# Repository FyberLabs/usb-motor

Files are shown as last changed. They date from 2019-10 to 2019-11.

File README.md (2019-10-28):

# usb-motor driver
Variation on the [Small Multicell USB Type C Charger](https://hackaday.io/project/85465-small-multicell-usb-type-c-charger), but with a specific purpose of making USB powered tools.
There will be a brushless version eventually and a few other application variations.
It supports a variety of rechargeable batteries and 1-4 cells depending on the solder bridge configuration.

For right now it has a single power/action button that can turn on/off, change speed, and reverse direction.
A capacitive trigger or other more precise control can be added.
There is also a reset button that can be removed after development.

These boards should 'mostly' stack in a 1x1.5" space with only a few wiring problems between them.
This design has excessive FET control and filtering which can be reduced.
Ideally, the design should fit on a single 1x1.5" board when developed for a specific application.

[Submitted gerbers to oshpark](https://oshpark.com/shared_projects/w56T8NJs])

front

back  

[Assembly BOM](http://htmlpreview.github.com/?https://github.com/FyberLabs/usb-motor/blob/master/bom/ibom.html)
Generated By [InteractiveHtmlBom](https://github.com/openscopeproject/InteractiveHtmlBom)  

GPL licensed firmware will be coming for the CCG3.  I expect to use stock TI firmware for TI chips.

Notes:
* There will be bugs in the hardware and eventually they will hopefully be found and 'fixed.
* There are many solderbridges to disable FET controls and select cell counts as necessary.
* The CC 5V line on CCG3 should be routed or the 3v3 supply made 5V to fully enable a powerbank/OTG capabilities.
* Initial testing of some of the boards, so some logic may be incorrect.
* Developed with extra small designator silkscreen fonts which are likely to fail most PCB processes.  
(They are not that important to my build process, and usually make a mess of the silkscreen either way.)
* First panel attempted through oshpark  
(Usually I remove edge lines on mousebites for other fabs, though this variation does make copper zones in KiCAD work better.)

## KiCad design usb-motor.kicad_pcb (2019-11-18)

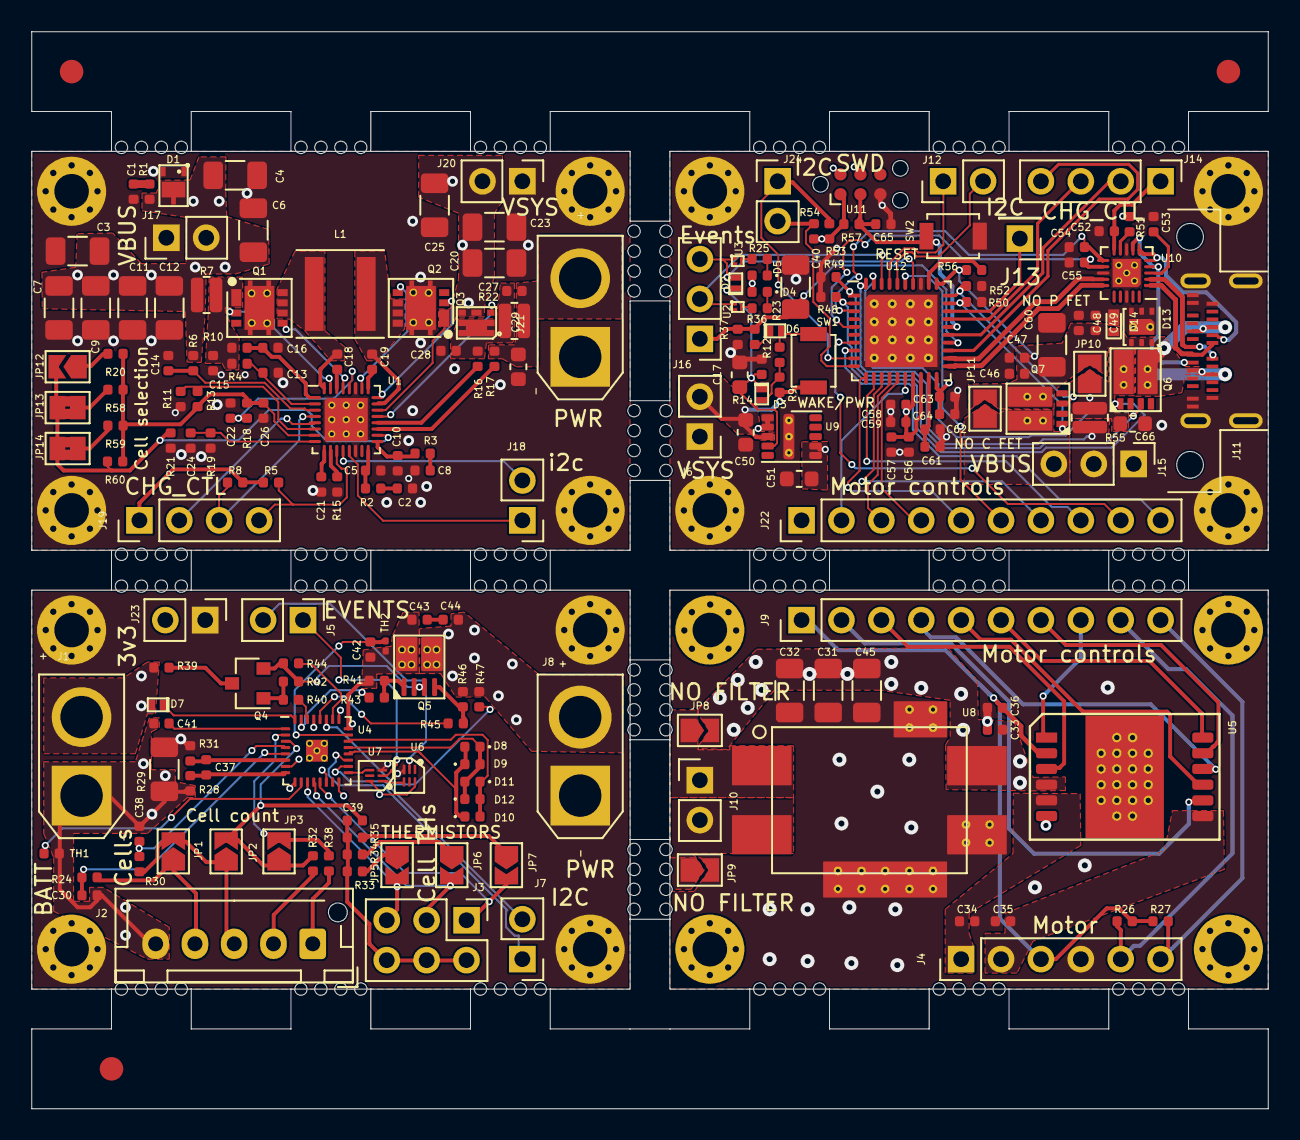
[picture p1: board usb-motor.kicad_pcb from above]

Board: 4 copper layers, 78.7 x 68.6 mm, 252 parts (0 on the bottom side), 128 nets.

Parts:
C1, C26, C28, C52, C57, C58, C61, C63: 1uF; C_0402_1005Metric
C2: 1800pF; C_0402_1005Metric
C3, C4, C6, C7, C9, C11, C12, C20, C23, C25, C31, C32, C40, C45: 22uF; C_1206_3216Metric
C5: 33pF; C_0402_1005Metric
C8: 680pF; C_0402_1005Metric
C10: 15pF; C_0402_1005Metric
C13, C14: 0.033uF; C_0402_1005Metric
C15, C46, C47, C48, C49: 0.01uF; C_0402_1005Metric
C16: 0.47uF; C_0402_1005Metric
C17, C29, C50: 10uF; C_0603_1608Metric
C18, C19: 0.047uF; C_0402_1005Metric
C21, C24: 100pF; C_0402_1005Metric
C22, C41: 2.2uF; C_0402_1005Metric
C27, C30, C33, C36, C37, C38, C39, C42, C43, C53, C56, C59, C62, C64, C65: 0.1uF; C_0402_1005Metric
C34, C35: 27nF; C_0402_1005Metric
C44: 0.22uF; C_0402_1005Metric
C51: 22uF+ 6.3V; C_0603_1608Metric
C54, C55: 390pF; C_0402_1005Metric
C60: 10uF; C_1206_3216Metric
C66: 1uF; C_0603_1608Metric
D1: ESDA22P150-1U3M; QFN-3 (ESDA22P150-1U3M)
D2, D3, D6, D7: BAS40LP-7; D_402
D4: VLMG1500-GS08; LED_0402_1005Metric
D5: VLMO1500-GS08; LED_0402_1005Metric
D8, D9, D10, D11, D12: VLMB1500-GS08; LED_0402_1005Metric
D13: TVS2200; TVS2200-DRV0006A-WSON-2x2
D14: NSR20F30NXT5G; DSN2(0603)
FID1, FID2, FID3: Fiducial; Fiducial_1.5mm_Mask3mm
H1, H2, H3, H4, H5, H6, H7, H8, H9, H10, H11, H12, H13, H14, H15, H16: M; MountingHole_2.2mm_M2_Pad_Via
J1: BATT; AMASS_XT30U-M_1x02_P5.0mm_Vertical
J2: Cells; JST_XH_B5B-XH-AM_1x05_P2.50mm_Vertical
J3: Cell THs; PinHeader_2x03_P2.54mm_Vertical
J4: Motor; PinHeader_1x06_P2.54mm_Vertical
J5: EVENTS; PinHeader_1x02_P2.54mm_Vertical
J6, J20: VSYS; PinHeader_1x02_P2.54mm_Vertical
J7, J12, J24: I2C; PinHeader_1x02_P2.54mm_Vertical
J8: PWR; AMASS_XT30U-F_1x02_P5.0mm_Vertical
J9, J22: Motor controls; PinHeader_1x10_P2.54mm_Vertical
J10: Power; PinHeader_1x02_P2.54mm_Vertical
J11: USB_C_Receptacle; USB_C_Receptacle_Amphenol_124018792112A
J13: xpins; PinHeader_1x01_P2.54mm_Vertical
J14, J19: CHG_CTL; PinHeader_1x04_P2.54mm_Vertical
J15: VBUS; PinHeader_1x03_P2.54mm_Vertical
J16: Events; PinHeader_1x03_P2.54mm_Vertical
J17: VBUS; PinHeader_1x02_P2.54mm_Vertical
J18: i2c; PinHeader_1x02_P2.54mm_Vertical
J21: PWR; AMASS_XT30U-M_1x02_P5.0mm_Vertical
J23: 3v3; PinHeader_1x02_P2.54mm_Vertical
JP1, JP2, JP3, JP5, JP6, JP7: SolderJumper_2_Open; SolderJumper-2_P1.3mm_Open_TrianglePad1.0x1.5mm
JP8, JP9: NO FILTER; SolderJumper-2_P1.3mm_Open_TrianglePad1.0x1.5mm
JP10: NO P FET; SolderJumper-2_P1.3mm_Open_TrianglePad1.0x1.5mm
JP11: NO C FET; SolderJumper-2_P1.3mm_Open_TrianglePad1.0x1.5mm
JP12: 4th; SolderJumper-2_P1.3mm_Open_TrianglePad1.0x1.5mm
JP13: 3rd; SolderJumper-2_P1.3mm_Bridged2Bar_Pad1.0x1.5mm
JP14: 2nd; SolderJumper-2_P1.3mm_Bridged2Bar_Pad1.0x1.5mm
L1: 2.2uH; L_Coilcraft_XAL5030
MOU1, MOU2, MOU3, MOU4, MOU5, MOU6, MOU7, MOU8, MOU9, MOU10, MOU11, MOU12, MOU13, MOU14, MOU15, MOU16, MOU17, MOU18, MOU19, MOU20, MOU21, MOU22, MOU23, MOU24, MOU25, MOU26, MOU27, MOU28, MOU29, MOU30, MOU31, MOU32: Mousebite; mousebites
Q1, Q2: CSD87333Q3D
Q3: FDMA6676PZ; MicroFET
Q4: FDN358P; SOT-23
Q5: CSD87313DMS
Q6, Q7: CSD87503Q3E
R1: 2.2 0.5W; R_0402_1005Metric
R2: 40.2k; R_0402_1005Metric
R3, R23, R25, R26, R27, R33, R34, R35, R36, R47: 10.0k; R_0402_1005Metric
R4, R6: 4.99; R_0402_1005Metric
R5, R8: 3.83k; R_0402_1005Metric
R7, R22, R55: 10m; KRL2012E(0508)
R9, R12: 270k; R_0402_1005Metric
R10: 1.0; R_0402_1005Metric
R11, R13, R14, R21, R37, R51: 100k; R_0402_1005Metric
R15: 30k; R_0402_1005Metric
R16, R17, R18: 10; R_0402_1005Metric
R19: 137k; R_0402_1005Metric
R20: 56-57k; R_0402_1005Metric
R24, R28, R30, R31, R32, R38, R44, R56: 100; R_0402_1005Metric
R29: 0.001; R_1206_3216Metric
R39: 300; R_0402_1005Metric
R40, R43, R45: 5.1k; R_0402_1005Metric
R41, R42, R46, R48, R49, R50, R52: 10.0M; R_0402_1005Metric
R53, R54: 2.2k; R_0402_1005Metric
R57: 4.7k; R_0402_1005Metric
R58: 169k; R_0402_1005Metric
R59: 280k; R_0402_1005Metric
R60: 300k; R_0402_1005Metric
SW1: WAKE/PWR; SW_SPST_B3U-1000P
SW2: RESET; SW_SPST_B3U-1000P
TH1: 103; R_0402_1005Metric
TH2: 10.0k; R_0201_0603Metric
U1: BQ25713(B); QFN-32_EP2.8_4x4_Pitch0.4mm
U2, U3: CSD15380F3; PICOSTAR (YJM)
U4: BQ4050R; QFN-32_EP1.4_4x4_Pitch0.4mm
U5: IFX9201SG; PG-DSO-12-17
U6: SN74LVC1G14D; TI-DSF0006A-SON-5P-SN74xx
U7: SN74LVC1G08D; TI-DSF0006A-SON-5P-SN74xx
U8: BNX02x
U9: LMZM23601V3; Texas_SIL0010A_MicroSiP-10-1EP_3.8x3mm_P0.6mm_EP0.7x2.9mm_T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
U10: TPD6S300A; QFN-20_EP1.8_3x3_Pitch0.4mm
U11: SWD; Tag-Connect_TC2030-IDC-NL_2x03_P1.27mm_Vertical
U12: CYPD3123-40LQXIT; QFN-40_EP_6x6_Pitch0.5mm

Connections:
+3V3: C51.2, C63.2, C64.2, D4.2, D5.2, J23.2, R51.2, U6.5, U7.5, U9.6, U9.7, U12.20
-BATT: C30.1, C38.1, C39.1, C41.1, J1.1, J2.5, J3.2, J3.4, J3.6, R28.2, R29.2, R33.1, R34.1, R35.1, TH1.2, U4.7, U4.9, U4.14, U4.16, U4.25, U4.29, U4.33
/4 Cell Charger/1c: J2.4, JP1.1, R24.2
/4 Cell Charger/2c: J2.3, JP1.2, JP2.1, R30.2
/4 Cell Charger/3c: J2.2, R32.2
/4 Cell Charger/BBAT: D7.1, U4.32
/4 Cell Charger/C43-44: C43.2, C44.1
/4 Cell Charger/CHG: R43.1, U4.31
/4 Cell Charger/DSG: R45.1, U4.28
/4 Cell Charger/JP5: JP5.1, R33.2
/4 Cell Charger/JP6: JP6.1, R34.2
/4 Cell Charger/JP7: JP7.1, R35.2
/4 Cell Charger/LEDA: D8.2, D9.1, D10.1, U4.20
/4 Cell Charger/LEDB: D8.1, D9.2, D11.2, D12.1, U4.21
/4 Cell Charger/LEDC: D10.2, D11.1, D12.2, U4.22
/4 Cell Charger/PACK: R47.2, U4.27
/4 Cell Charger/PBI: C41.2, U4.1
/4 Cell Charger/PCHG: R40.2, U4.30
/4 Cell Charger/PTC: C42.1, TH2.1, U4.23
/4 Cell Charger/R39: Q4.3, R39.1
/4 Cell Charger/R40: Q4.1, R40.1, R42.1
/4 Cell Charger/R43: Q5.1, R41.1, R43.2
/4 Cell Charger/R45: Q5.4, R45.2, R46.1
/4 Cell Charger/SRN: C37.1, R31.1, U4.6
/4 Cell Charger/SRP: C37.2, R28.1, U4.8
/4 Cell Charger/TS1: TH1.1, U4.10
/4 Cell Charger/TS2: J3.5, JP5.2, U4.11
/4 Cell Charger/TS3: J3.3, JP6.2, U4.12
/4 Cell Charger/TS4: J3.1, JP7.2, U4.13
/4 Cell Charger/VC1: C30.2, R24.1, U4.5
/4 Cell Charger/VC2: C38.2, R30.1, U4.4
/4 Cell Charger/VC3: C39.2, JP2.2, JP3.1, R32.1, U4.3
/4 Cell Charger/VC4: JP3.2, R38.1, U4.2
/4 Cell Charger/VCCQ: Q4.2, Q5.2, Q5.3, R42.2, R44.2
/4 Cell Charger/VCCcell: R44.1, U4.26
/4 Cell Charger/~DISP: U4.17, U7.4
/4 Cell Charger/~SW_SIG: U6.4, U7.1
/6-36V: C42.2, C43.1, D7.2, J1.2, J2.1, J10.1, JP8.1, Q5.8, R38.2, R39.2, R41.2, TH2.2, U4.24, U8.B
/BAT_OUT: C27.2, C29.1, C44.2, J8.2, J21.2, Q5.5, R17.1, R22.1, R46.2, R47.1
/Brushed 12V Motor/36V: C31.2, C32.1, C33.1, C45.2, JP8.2, U5.4, U8.CB
/Brushed 12V Motor/GNDF: C31.1, C32.2, C33.2, C34.2, C35.2, C36.2, C45.1, J4.4, JP9.2, U5.6, U8.CG
/Brushed 12V Motor/M1: C34.1, J4.1, U5.5
/Brushed 12V Motor/M2: C35.1, J4.2, U5.7
/CHRG_OK: J14.3, J19.3, R8.1, U1.4, U12.27
/CSN: J9.5, J22.5, U5.9, U12.11
/DIR: J9.8, J22.8, U5.1, U11.4, U12.12
/DIS: J9.7, J22.7, U5.11, U11.2, U12.13
/EN_OTG: J14.2, J19.2, U1.5, U12.25
/GPIO13: J13.1, U12.28
/PROCHOT: J14.4, J19.4, R5.1, U1.11, U12.23
/PWM: J9.6, J22.6, U5.12, U12.35
/SCK: J9.4, J22.4, U5.10, U12.15
/SCL: J7.1, J18.1, J24.1, R53.2, U1.13, U4.19, U12.9
/SDA: J7.2, J18.2, J24.2, R54.2, U1.12, U4.18, U12.10
/SENSA: J4.5, J9.9, J22.9, R26.2, U12.7
/SENSB: J4.6, J9.10, J22.10, R27.2, U12.8
/SI: J9.2, J22.2, U5.8, U12.16
/SNK_EVENT: D2.2, J5.1, J16.3, U3.1, U7.2, U12.34
/SO: J9.3, J22.3, U5.3, U12.14
/SW_SIG: C40.2, J5.2, J16.1, R36.2, R37.1, U6.2, U12.24
/USB Buck Boost/ACN: C13.1, R4.1, U1.2
/USB Buck Boost/ACP: C14.1, R6.1, U1.3
/USB Buck Boost/CELL_PREZ: JP12.2, JP13.2, JP14.2, R21.1, R60.2, U1.18
/USB Buck Boost/COMP1: C5.1, R2.2, U1.16
/USB Buck Boost/COMP1T: C2.1, R2.1
/USB Buck Boost/COMP2: C10.1, R3.2, U1.17
/USB Buck Boost/COMP2TT: C8.1, R3.1
/USB Buck Boost/HIDRV1: Q1.3, U1.31
/USB Buck Boost/HIDRV2: Q2.3, U1.24
/USB Buck Boost/IADPT: C24.1, R19.1, U1.8
/USB Buck Boost/IBAT: C21.1, U1.9
/USB Buck Boost/ILIM: R11.1, R13.1, U1.6
/USB Buck Boost/JP12: JP12.1, R20.2
/USB Buck Boost/JP13: JP13.1, R58.2
/USB Buck Boost/JP14: JP14.1, R59.2
/USB Buck Boost/LODRV1: Q1.5, U1.29
/USB Buck Boost/LODRV2: Q2.5, U1.26
/USB Buck Boost/PSYS: R15.1, U1.10
/USB Buck Boost/REGN: C22.1, R18.2, U1.28
/USB Buck Boost/SRN: R17.2, U1.19
/USB Buck Boost/SRP: R16.2, U1.20
/USB Buck Boost/SRP_R: C27.1, C28.1, Q3.1, Q3.2, Q3.5, Q3.6, Q3.8, R16.1, R22.2
/USB Buck Boost/SW1: C18.1, L1.1, Q1.6, Q1.7, Q1.8, U1.32
/USB Buck Boost/SW2: C19.1, L1.2, Q2.6, Q2.7, Q2.8, U1.23
/USB Buck Boost/TST1: C18.2, U1.30
/USB Buck Boost/TST2: C19.2, U1.25
/USB Buck Boost/VBUS_D: C1.2, R1.1
/USB Buck Boost/VBUS_IN: C16.1, R10.2, U1.1
/USB Buck Boost/VBUS_VIN: C15.1, Q1.1, Q1.2, R4.2, R7.1, R10.1
/USB Buck Boost/VDDA: C26.1, R13.2, R18.1, R20.1, R58.1, R59.1, R60.1, U1.7
/USB Buck Boost/~BATDRV: Q3.3, U1.21
/USB PD/CC1: C55.2, U10.12, U12.5
/USB PD/CC2: C54.1, U10.11, U12.3
/USB PD/C_CC1: J11.A5, U10.4, U10.7
/USB PD/C_CC2: J11.B5, U10.5, U10.6
/USB PD/D4: D4.1, R23.1
/USB PD/D5: D5.1, R25.1
/USB PD/D6: D6.1, R36.1
/USB PD/DN: J11.A7, J11.B7, U10.2
/USB PD/DP: J11.A6, J11.B6, U10.1
/USB PD/H_DN: U10.14, U12.22
/USB PD/H_DP: U10.15, U12.21
/USB PD/OC: C66.2, JP10.1, Q6.8, R55.2, U12.39
/USB PD/R23: R23.2, U2.3
/USB PD/R25: R25.2, U3.3
/USB PD/SRC_EVENT: J16.2, U2.1, U12.38
/USB PD/SW: D6.2, R12.1, SW1.2
/USB PD/SW_EN: D3.2, R9.2, R12.2
/USB PD/SW_S_EN: C17.1, D2.1, D3.1, R14.1, U9.4
/USB PD/VBIAS: C53.2, U10.3
/USB PD/VBUS_C_C0: Q7.3, R52.2, U12.30
/USB PD/VBUS_C_C1: Q7.1, R50.2, U12.29
/USB PD/VBUS_P_C0: Q6.1, R48.2, U12.2
/USB PD/VBUS_P_C1: Q6.3, R49.2, U12.1
/USB PD/VCCD: C61.2, C62.2, U12.19
/USB PD/VDISCHG: R56.2, U12.32
/USB PD/XRES: C65.2, R57.1, SW2.1, U11.3, U12.26
/USB PD/~FLT: R51.1, U10.9
/VBUS: C3.1, C4.1, C6.1, C7.1, C9.1, C11.1, C12.1, D1.1, J15.2, J17.2, R1.2, R6.2, R7.2, R55.1, U12.40
/VBUS_C: J15.3, JP11.1, Q7.8
/VDDD: C36.1, C52.2, C56.2, C57.2, C58.2, C59.2, J4.3, J9.1, J14.1, J19.1, J22.1, R5.2, R8.2, R26.1, R27.1, R53.1, R54.1, R57.2, U5.2, U10.10, U11.1, U12.17, U12.18
/VSYS: C20.1, C23.1, C25.1, C50.2, J6.2, J20.2, Q2.1, Q2.2, Q3.4, Q3.7, R9.1, SW1.1, U1.22, U9.3
/X_SCL: J12.1, U12.37
/X_SDA: J12.2, U12.36
GND: C1.1, C2.2, C3.2, C4.2, C5.2, C6.2, C7.2, C8.2, C9.2, C10.2, C11.2, C12.2, C13.2, C14.2, C15.2, C16.2, C17.2, C20.2, C21.2, C22.2, C23.2, C24.2, C25.2, C26.2, C28.2, C29.2, C40.1, C46.1, C47.1, C48.1, C49.1, C50.1, C51.1, C52.1, C53.1, C54.2, C55.1, C56.1, C57.1, C58.1, C59.1, C60.1, C61.1, C62.1, C63.1, C64.1, C65.1, C66.1, D1.2, D13.2, D14.2, H1.1, H2.1, H3.1, H4.1, H5.1, H6.1, H7.1, H8.1, H9.1, H10.1, H11.1, H12.1, H13.1, H14.1, H15.1, H16.1, J6.1, J8.1, J10.2, J11.A1, J11.A12, J11.B1, J11.B12, J11.S1, J15.1, J17.1, J20.1, J21.1, J23.1, JP9.1, Q1.9, Q2.9, R11.2, R14.2, R15.2, R19.2, R21.2, R29.1, R31.2, R37.2, R48.1, R49.1, R50.1, R52.1, SW2.2, U1.14, U1.27, U1.33, U2.2, U3.2, U6.3, U7.3, U8.PSG, U9.1, U9.2, U9.11, U10.8, U10.13, U10.18, U10.21, U11.5, U12.33, U12.41
unnamed: Q6.2, Q6.4
unnamed: Q7.2, Q7.4
PRI_HI: C46.2, C47.2, C48.2, C49.2, C60.2, D13.1, D14.1, J11.A4, J11.A9, J11.B4, J11.B9, JP10.2, JP11.2, Q6.5, Q7.5, R56.1, U12.31

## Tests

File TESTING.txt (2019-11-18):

T5 is too small possibly.  A lot of solder bridges, but the assembly took 7 hours...
RMCF0402JT100R replaced by RC0402FR-07100RL
NCP03XH103E05RL convert to 0402?
10 more VLMB1500-GS08 than ordered, probably reversed them all… datasheet is horrible
Redo motor board with smaller/correct IFX9201SGAUMA1 footprint
Brushed Motor board will be specially refabbed at 0.3.0-b.

Design looks mostly good on fab of 0.3a.
Trying T5 paste for flow through stencil small pads.
May need to widen paste stencils for small pads or switch components.

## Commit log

2019-09-06 initial public commit
    [4cellcharger.sch, Brushed12Vmotor.sch, USBBuckBoost.sch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]
2019-09-07 added some design notes
    [usb-motor.kicad_pcb]
2019-10-28 Post fab edits for assembly
    [4cellcharger.sch, Brushed12Vmotor.sch, USBBuckBoost.sch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]
2019-10-28 Add assembly bom link
2019-10-28 fix cells dup name
    [4cellcharger.sch, USBPD.sch, usb-motor.kicad_pcb]
2019-11-18 post fab error fixes, brushed motor needs refabbed.
    [USBPD.sch, usb-motor.kicad_pcb]
